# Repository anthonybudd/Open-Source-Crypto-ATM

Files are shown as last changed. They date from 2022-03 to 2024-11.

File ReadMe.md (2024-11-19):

# OSCA - Open-Source Crypto ATM

The Open-Source Crypto ATM, a Bitcoin ATM that someone with minimal electro-mechanical skill can build at home with parts from Amazon and hardware from Lowes. OSCA does not require you to disclose any personal information to use this ATM. The user inserts cash and the machine returns a cold wallet loaded with the desired amount of crypto-currency.

<p align="center">
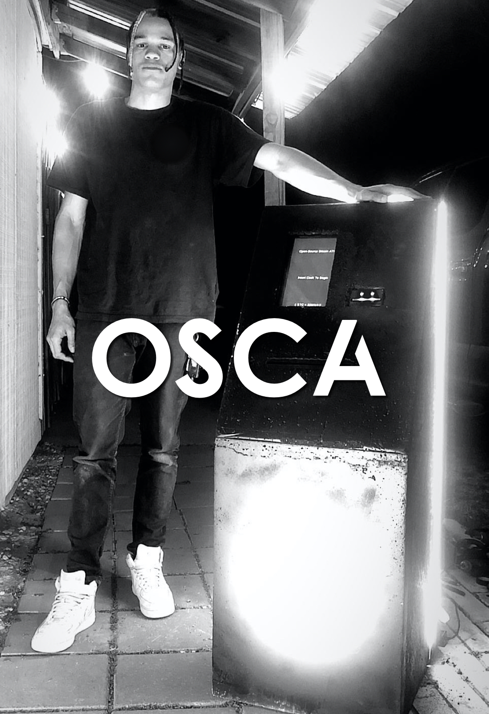
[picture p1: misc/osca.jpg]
OSCA
    
</p>

### Instructions
Detailed step-by-step instructions and a video tutorial are coming soon. However you can find all of the software and plans in this repo.
- [Build Instructions](https://github.com/anthonybudd/Open-Source-Crypto-ATM/blob/master/instructions/Instructions.md)

### Usecases

- Accept Bitcoin - Want to accept Bitcoin at your business? Use OSCA to provide your customers a easy way to purchase Bitcoin

- Passive Income - Use the commission feature to earn a commission on each transaction.
  
- Fungibility - Make crypto more fungibile by allowing anyone to anonymously convert hard fiat currency into cryptocurrency.

### How does it work?

OSCA is very simple to use. Simply insert the amount of cash you would like converted to Bitcoin then press the blue flashing button. 

<p align="center">
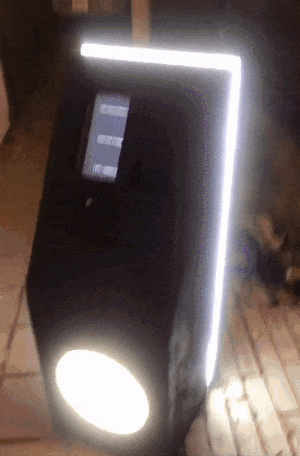
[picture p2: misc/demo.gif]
Demo
    
</p>

A paper wallet will be printed that is loaded with the desired amount of Bitcoin. Scan the status QR code to see your transaction on blockchain. Scan the withdraw QR code on the right to sweep the paper wallet. 

<p align="center">
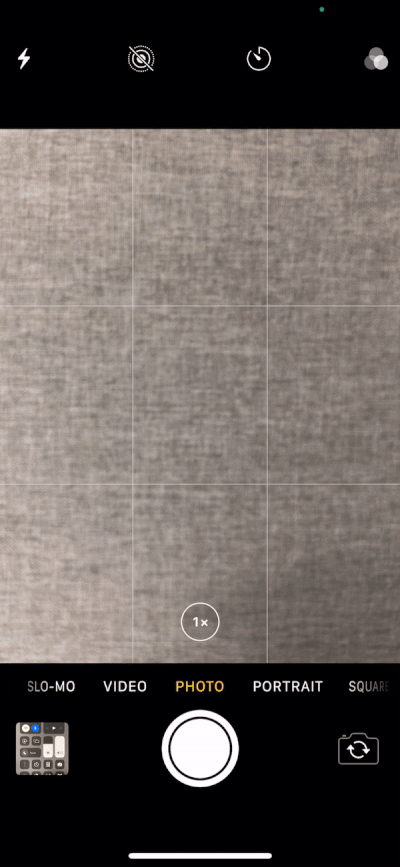
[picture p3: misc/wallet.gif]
    
</p>

### Motivation

Bitcoin and crypto in general have the power to revolutionise finance. However anonymously converting fiat currency into crypto is becoming harder and harder. All of the major crypto exchanges require disclosure of personal identifiable information. Even the Bitcoin ATMs at your local gas station require a cell phone number and an email address. Crypto-currencies are so much of a threat to the legacy banking system that the UK has banned Bitcoin ATMs outright. This concerns me because I believe if we remain on this course open-source technology like blockchain will become heavily regulated and corporatized.

The Open-Source Crypto ATM aims to remedy these issues by making it safe, easy and anonymous for anyone to convert hard fiat currency into digital cryptocurrency. The machine has been deliberately designed so someone with minimal electro-mechanical skill can build this ATM at home with a few off the shelf electronics and trip to the local hardware store.

By making this project open-source I hope others will contribute to this project and extend the software to work with other popular crypto-currencies. Over the long-term I hope that anonymous crypto ATMs will make crypto more accessible and fungible.

### FAQ

#### How can I trust this machine?

**YOU CAN’T**. I’ll say that again, you can’t trust this machine if you see it in the wild. A malicious actor could simply not load the paper wallet or save a copy of each private key it generates. So why build it then? My vision is that in the short to medium-term these kind of machines will be operated by independent businesses (gas stations, gun stores, smoke shops, etc) and the customers will trust the operator, not the machine per se. A user can easily test if the wallet is being loaded or not with a $5 transaction. Always remember to withdraw the value of the paper wallet to a secure wallet as soon as possible.

#### Why use paper wallets?

Paper wallets are controversial because they are considered outdated and unsecure, however I believe this is a perfect use case. While admittedly they have their drawbacks, paper wallets allow for the most anonymous method of exchanging cash for cryptocurrency. Any digital method could potentially expose the identity of the recipient. Furthermore any digital method of exchange would require the user to have a smartphone to use this machine, which not everybody has. I see no reason why cryptocurrencies must exist exclusively in the digital domain.

#### Why use concrete not metal?

Consider the Venn diagram of the parameters of this project. A) It must be easy to build B) Require minimal skill to build C) Must be cheap and extremely robust. While metal has obvious advantages (not least of which aesthetic), it requires skill to work with and expensive tools. Concrete is very cheap, it’s easy to work with and is exceptionally strong. Therefore concrete is the obvious choice.

#### Why Bitcoin? Why not Monero or Ethereum?

For better or for worse Bitcoin is the poster-child cryptocurrency. Its over a decade old, I bet your grandparents have heard about it at this point. Therefore I feel like that was the best cryptocurrency to start with.

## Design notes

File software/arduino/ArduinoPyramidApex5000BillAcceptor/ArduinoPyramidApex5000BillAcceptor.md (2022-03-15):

# ArduinoPyramidApex5000

This is a small program for using the Apex Pyramid 5000 bill acceptor via Serial.

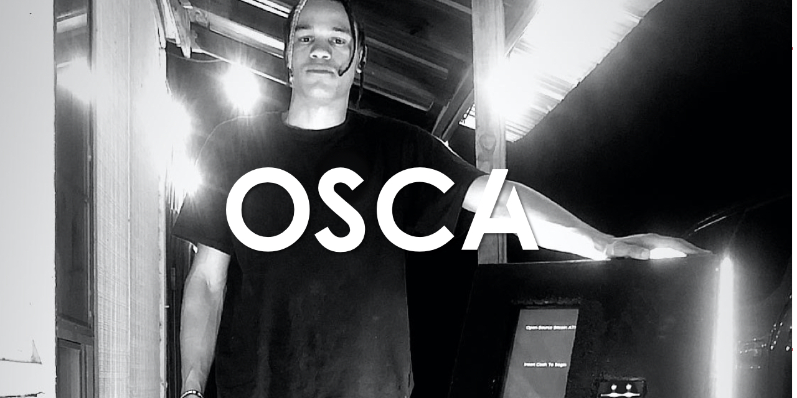
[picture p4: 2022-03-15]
misc/repo.jpg

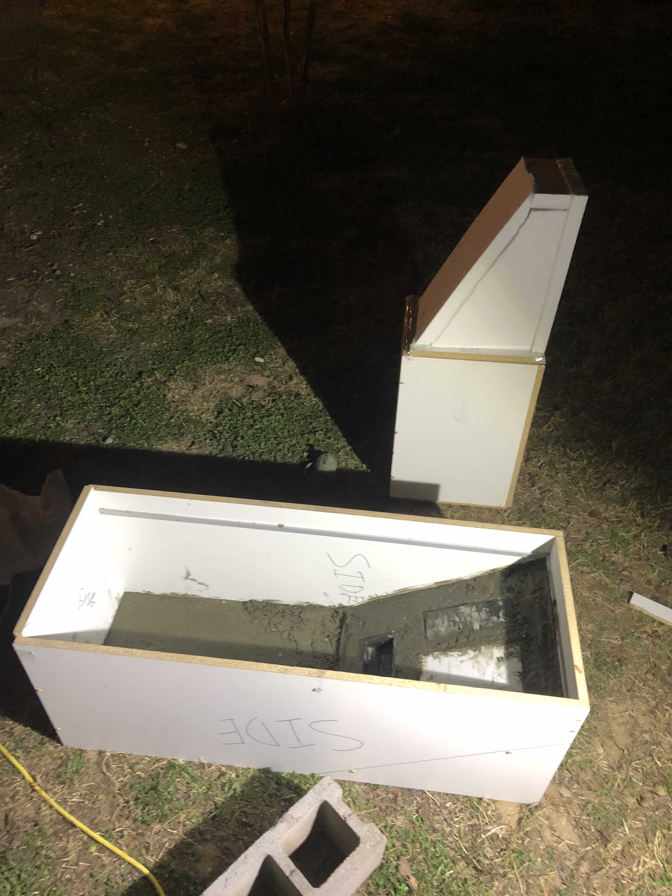
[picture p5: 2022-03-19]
misc/interior-and-exterior-mold.jpg

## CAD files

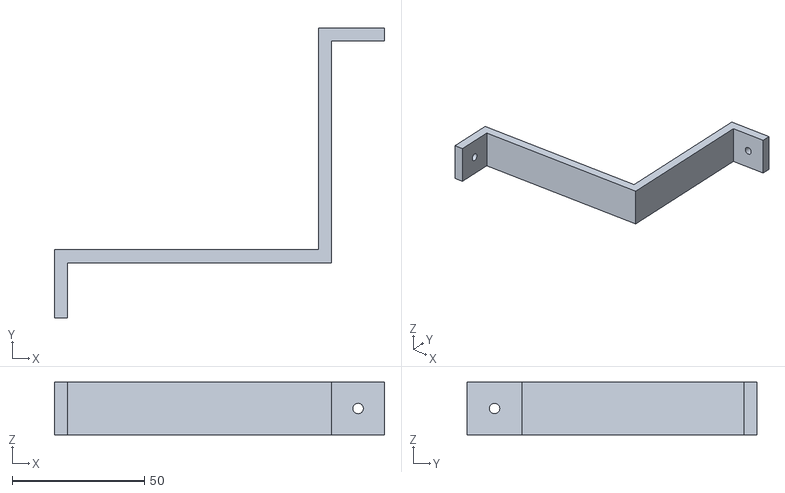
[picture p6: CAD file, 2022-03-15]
instructions/parts/Bill Accepter/Bill-Accepter-retention-arm.stl
125.0 x 109.9 x 20.0

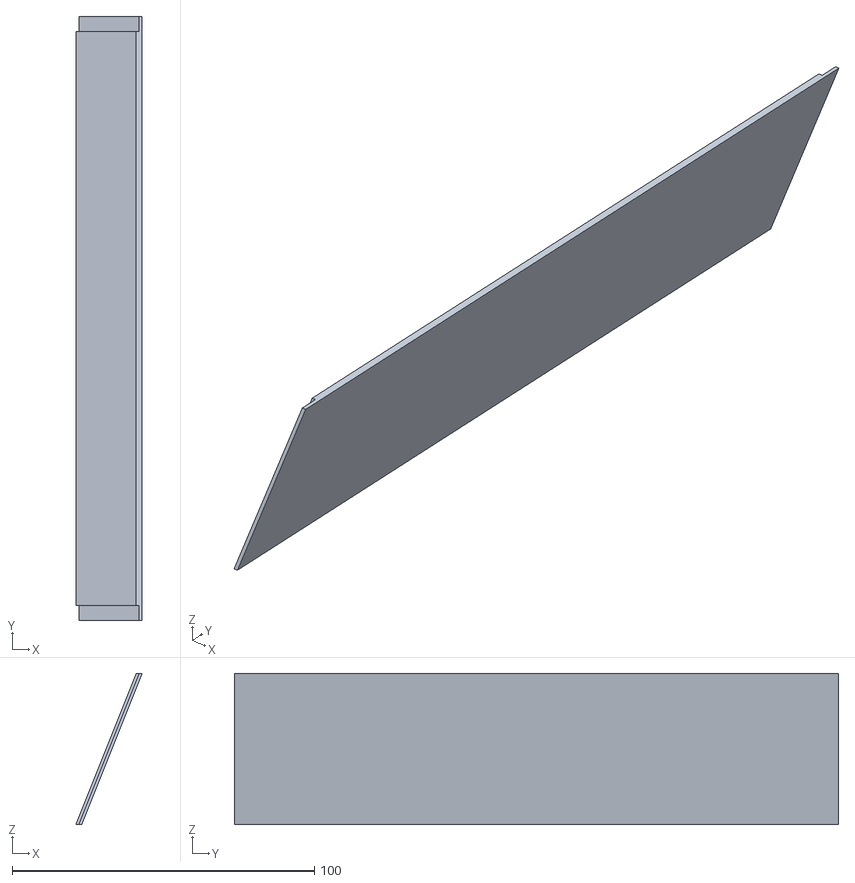
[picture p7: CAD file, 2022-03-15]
instructions/parts/Door/Side Inverted.stl
22.0 x 200.0 x 50.0

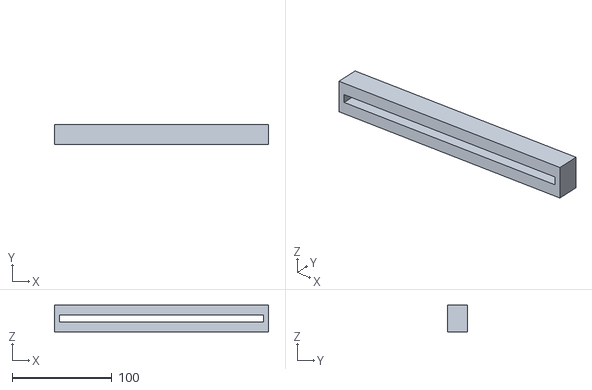
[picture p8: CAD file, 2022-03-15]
instructions/parts/Rollo/Rollo-Mouth.stl
215.0 x 20.0 x 27.0

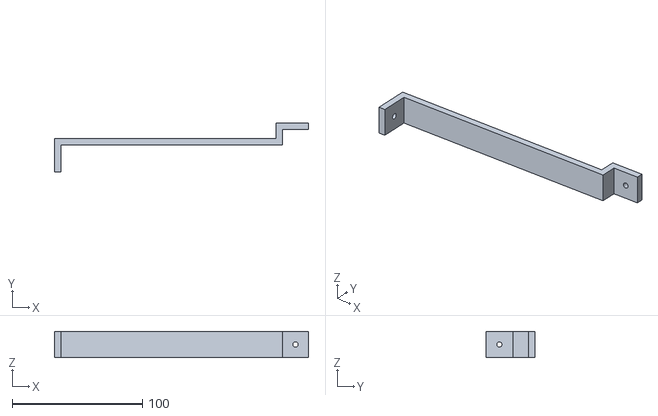
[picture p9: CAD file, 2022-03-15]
instructions/parts/Screen/Screen Retention Arm.stl
195.0 x 37.9 x 20.0

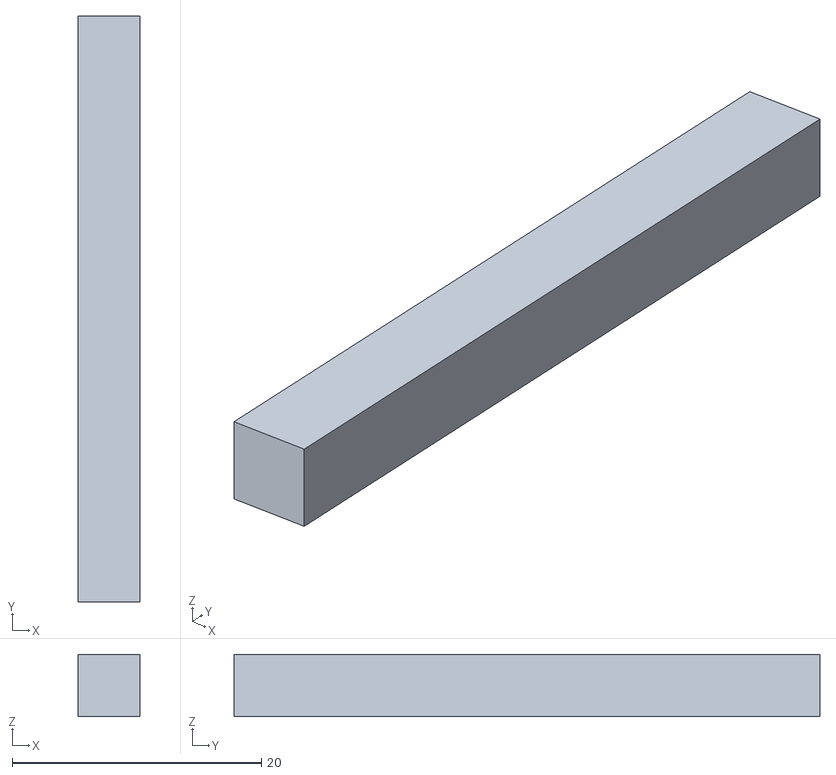
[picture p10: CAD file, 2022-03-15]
instructions/parts/Bill Accepter/bill accepter mold stand off.stl
5.00 x 47.0 x 5.00

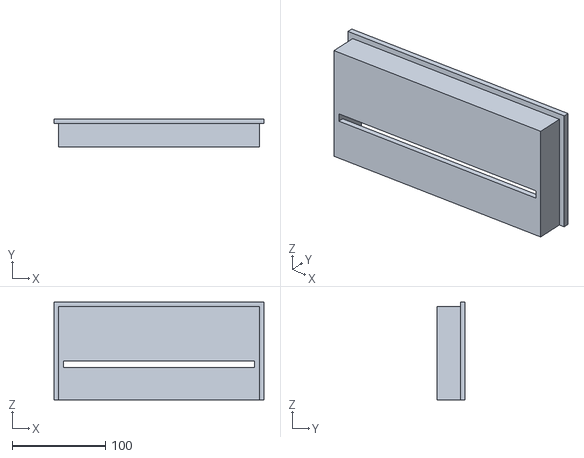
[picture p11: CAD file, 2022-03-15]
instructions/parts/Rollo/Rollo.stl
225.0 x 30.0 x 105.0

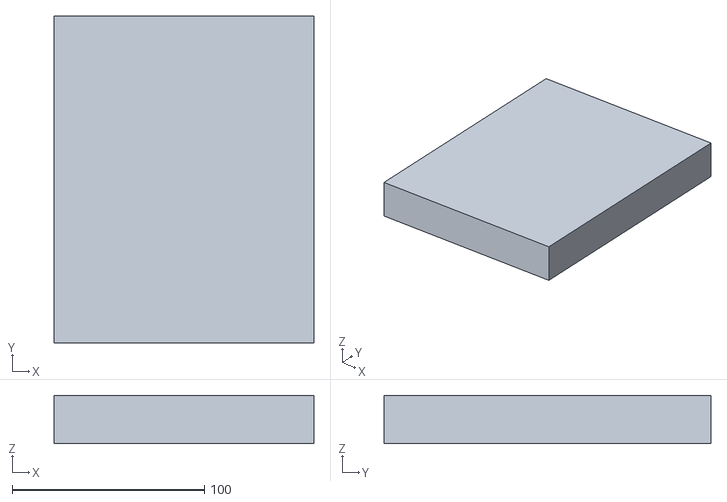
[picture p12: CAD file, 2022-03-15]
instructions/parts/Screen/screen mold.stl
135.0 x 170.0 x 25.0

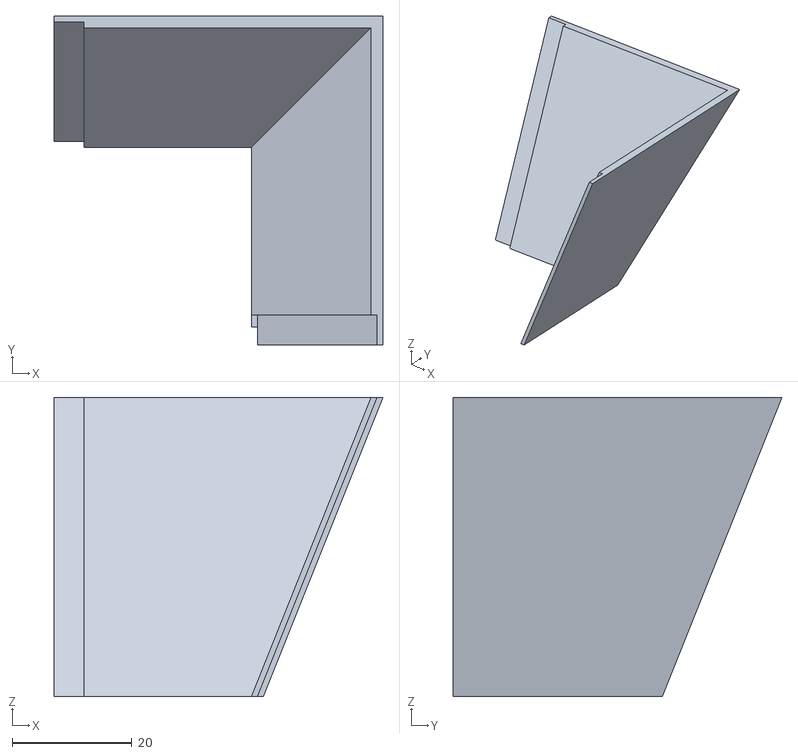
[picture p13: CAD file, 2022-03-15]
instructions/parts/Door/Corner.stl
55.0 x 55.0 x 50.0

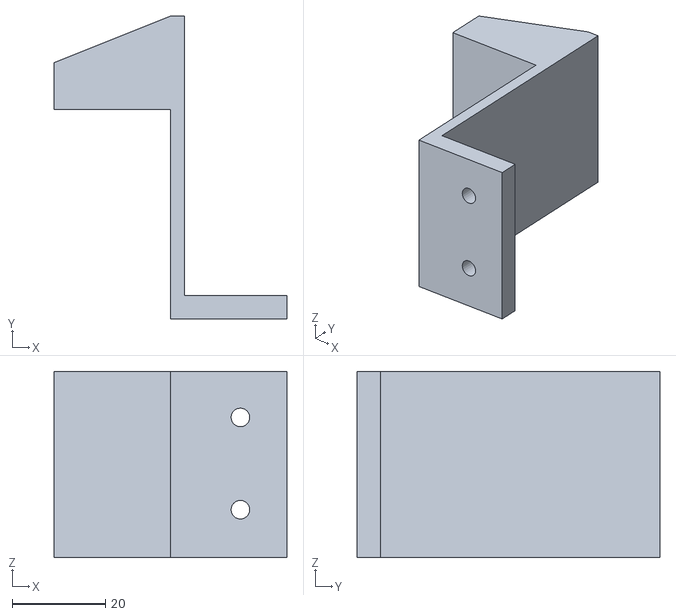
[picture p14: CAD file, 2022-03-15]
instructions/parts/Rollo/Rollo clip -10mm.stl
50.0 x 65.0 x 40.0

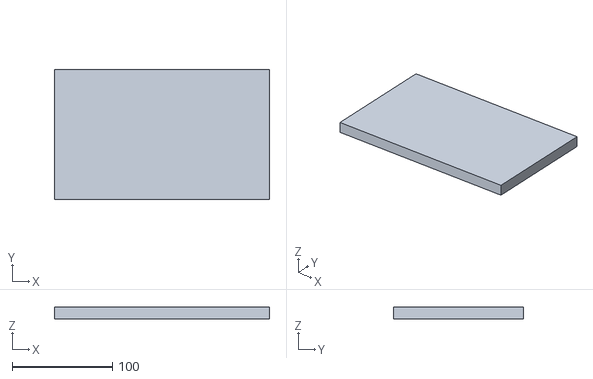
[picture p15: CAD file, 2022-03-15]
instructions/parts/Screen/viewport mold.stl
215.0 x 130.0 x 12.0

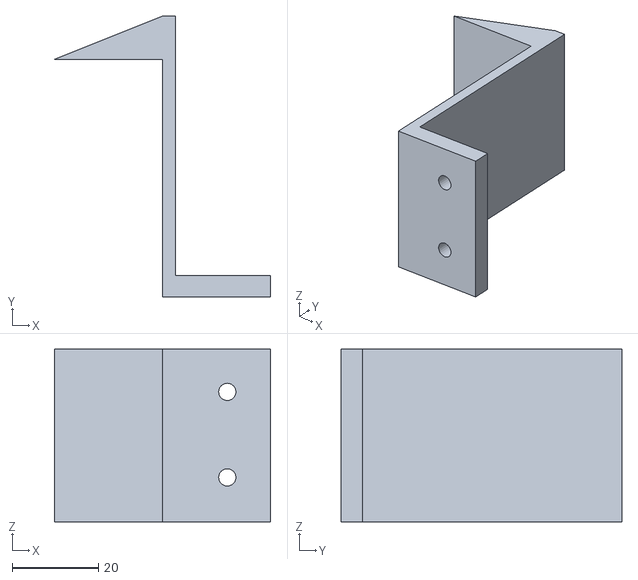
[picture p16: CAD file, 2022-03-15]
instructions/parts/Rollo/Rollo Retention Clip.stl
50.0 x 65.0 x 40.0

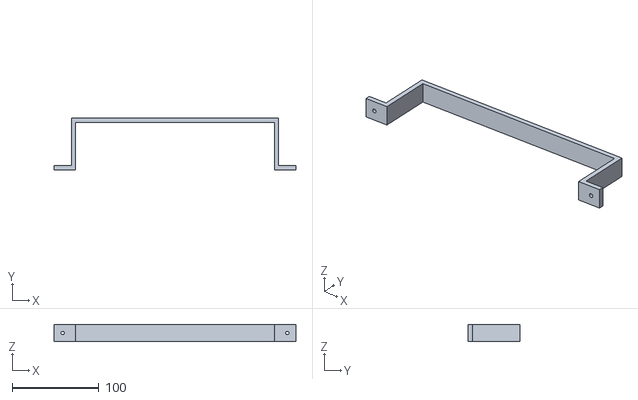
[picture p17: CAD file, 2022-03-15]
instructions/parts/Rollo/Rollo Retention Arm.stl
279.0 x 60.0 x 20.0

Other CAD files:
instructions/parts/Door/Side.stl
instructions/parts/Rollo/Rollo clip -5mm.stl
instructions/Case.skp
instructions/Case~.skp
instructions/parts/Bill Accepter/Bill Accepter.skp
instructions/parts/Bill Accepter/Bill-Accepter-retention-arm.skp
instructions/parts/Bill Accepter/Bill-Accepter-retention-arm~.skp
instructions/parts/Door/Corner.skp
instructions/parts/Door/Corner~.skp
instructions/parts/Rollo/Rollo.skp
instructions/parts/Rollo/Rollo~.skp
instructions/parts/Screen/Screen Retention Arm.skp
instructions/parts/Screen/Screen Retention Arm~.skp
instructions/parts/Screen/screen mold.skp
instructions/parts/Screen/viewport mold.skp
instructions/parts/Screen/viewport mold~.skp

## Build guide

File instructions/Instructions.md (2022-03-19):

# Instructions
*Detailed step by step instructions and a video tutorial are coming soon.*

I will be writing more detailed instructions as I develop this project. Below is a brief overview on how you can build an OSCA machine.

<!-- 
### Parts
| Name        | Price | Link |
| ----------- | ----- ------ | ----------- |
| Pyramid APEX 7000       | $200       |  |
| Paragraph   | Text        |  |

### Tools
| Name | Price | Link |
| --- | --- | --- |
| Pyramid APEX 7000 | $200 |  |
| Paragraph | Text |  | -->

### Phase 1
I recommend that you build OSCA using the same three phase approach I developed it. First buy the electronics and test the software, second build the cast and pour the concrete, finally mount the electronics and paint.

#### Arduino and Bill Acceptor
First load the provided Arduino sketch onto the Arduino nano. Connect the button  and the Apex 7000 bill acceptor as shown in the provided schematic.

Using the Arduino IDE serial monitor test that the Arduino is outputting the expected strings. Insert a bill into the bill acceptor and you should see the dollar amount display on the serial monitor. When you press the button the serial monitor should display the string “RESET”

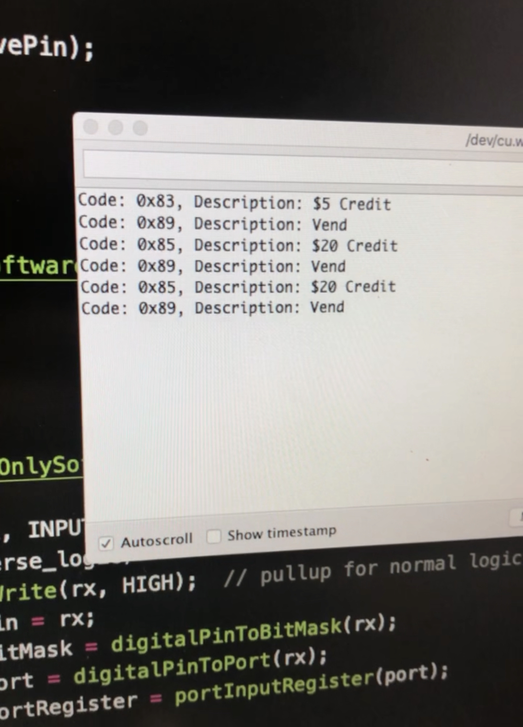
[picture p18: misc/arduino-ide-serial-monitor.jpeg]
Arduino IDE serial monitor


#### Pi
Run the provided bash commands provided in [App.md](https://github.com/anthonybudd/Open-Source-Crypto-ATM/blob/master/software/app/App.md) to set up your Pi and make the python script auto-run.

#### Printer/CUPS
Install cups and install the provided rollo Linux driver. Do a test print using the CLI and an example 4x6 label pdf to confirm that the printer is correctly set-up.
`lp -h localhost:631 ~/test.pdf`

#### Cellular Router
Insert a sim into the cellular router and connect the LAN 2 port to the raspberry Pi’s Ethernet port. Confirm that you have a internet connection by visiting a website using the pi’s browser.

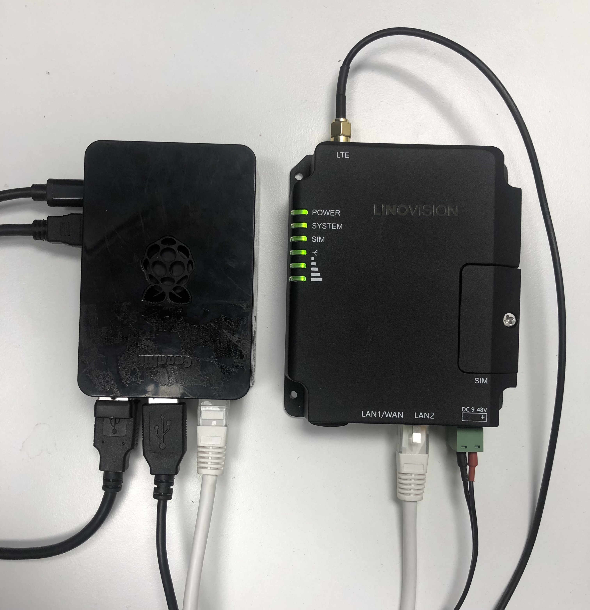
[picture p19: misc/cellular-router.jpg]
Cellular router and Pi


*I will be addressing the need for a 4G device in a upcoming project*

#### Battery
Connect all of the electronics to the battery and test that the system can power up, connect to the internet, boot the python GUI and it can successfully make a transaction.

### Phase 2
Go to your local hardware store and buy 3/4 lined 8x4 wood sheets. Have the store cut the wood as shown in the [provided designs](https://github.com/anthonybudd/Open-Source-Crypto-ATM/blob/master/instructions/case.png). 

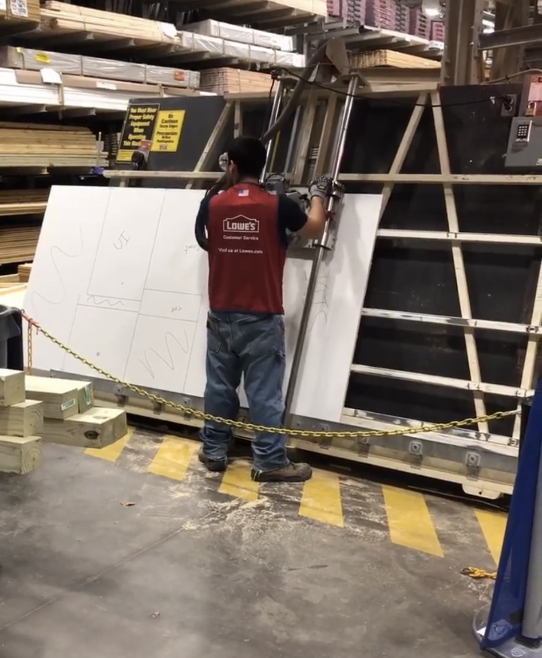
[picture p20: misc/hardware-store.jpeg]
Harware Store


Using a 3D printer print the casting parts for the machine. Use a hot glue gun to stick the molds to the internal side of the UI face.

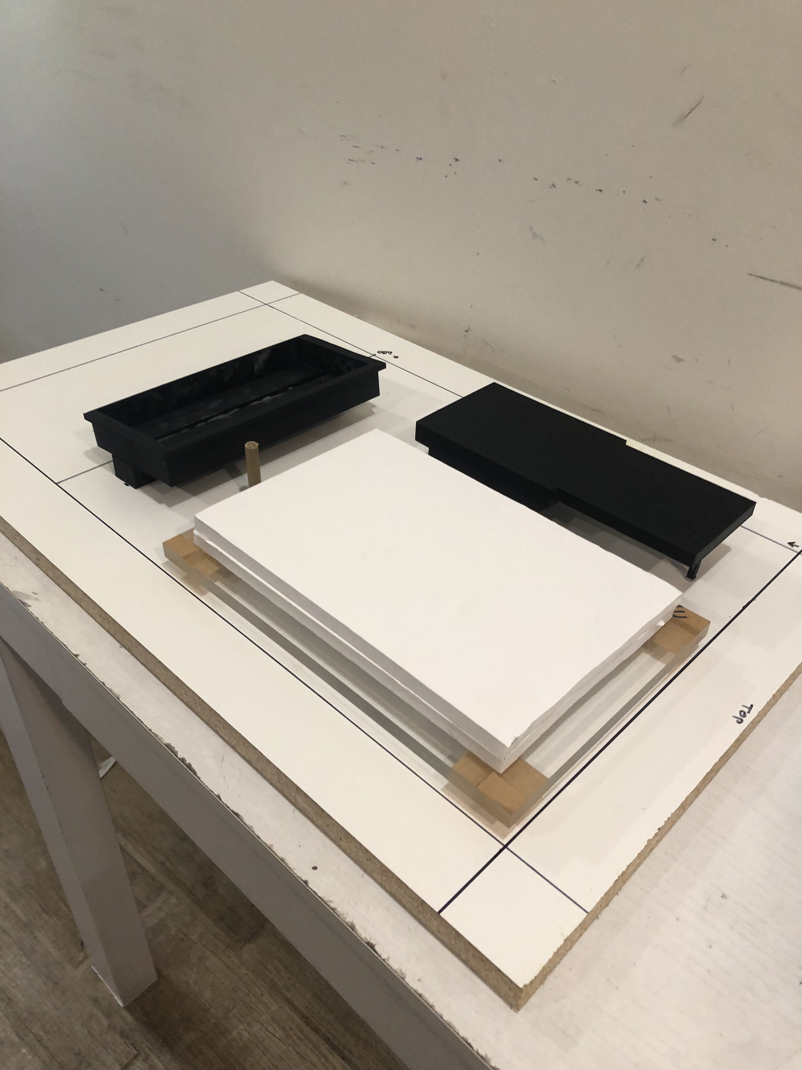
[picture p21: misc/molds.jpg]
3D Printed Molds


Screw the wood together to form the outer cast. 

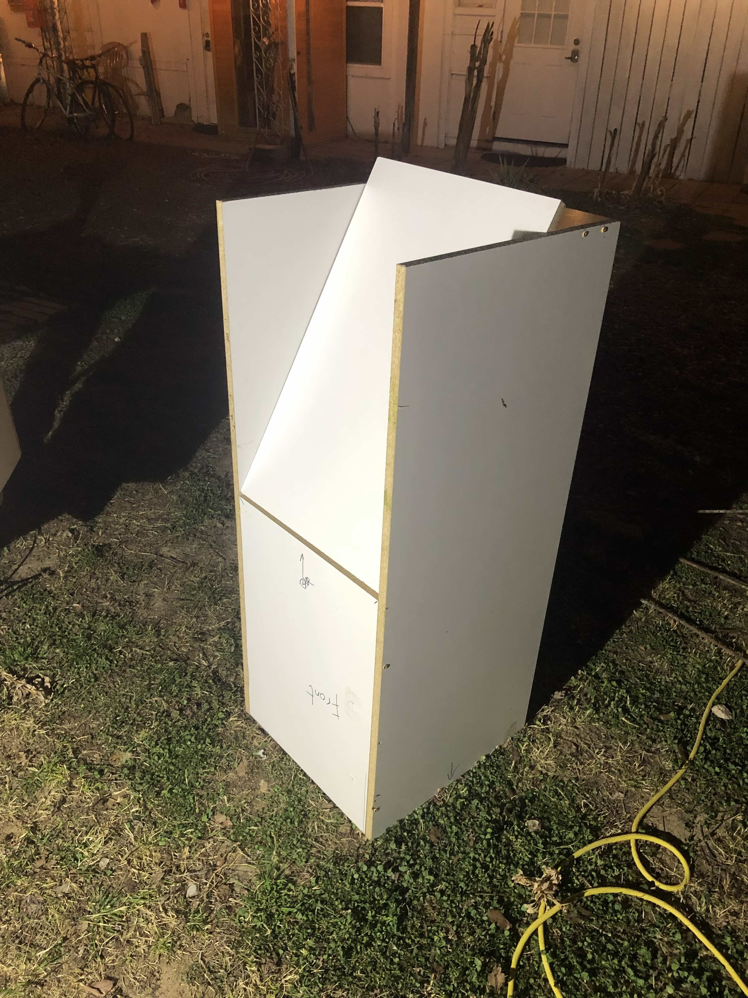
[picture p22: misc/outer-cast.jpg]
Outer Cast


Screw the interior mold together and glue on the polystyrene foam insert.

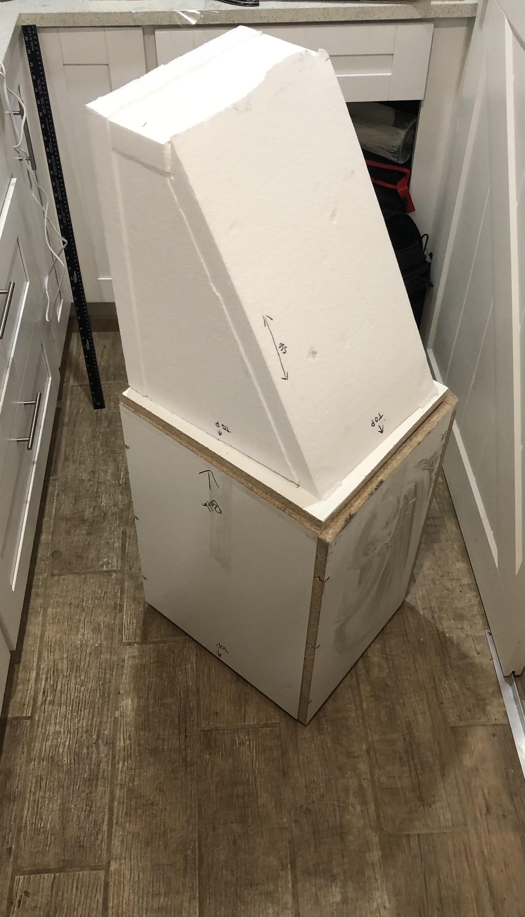
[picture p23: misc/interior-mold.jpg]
Interior Mold


Mix the concrete, start by packing the concrete into the small areas between the 3d printed molds. Wait an hour for the UI face to begin to set then lay the concrete for the front face.

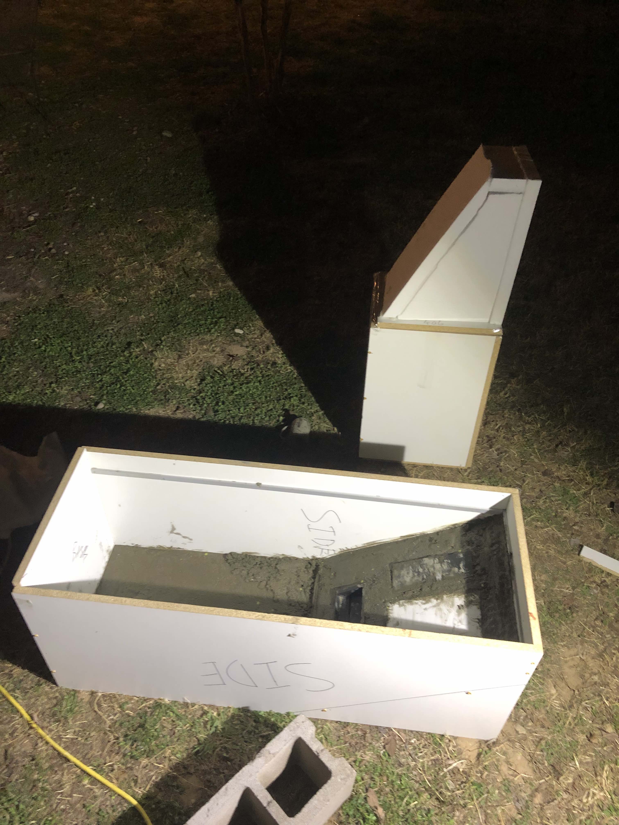
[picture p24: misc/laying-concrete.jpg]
First Concrete


Finally insert the interior mold into the exterior mold and fill the remainiung space with concrtete. Wait 24 hours for the cast to dry.

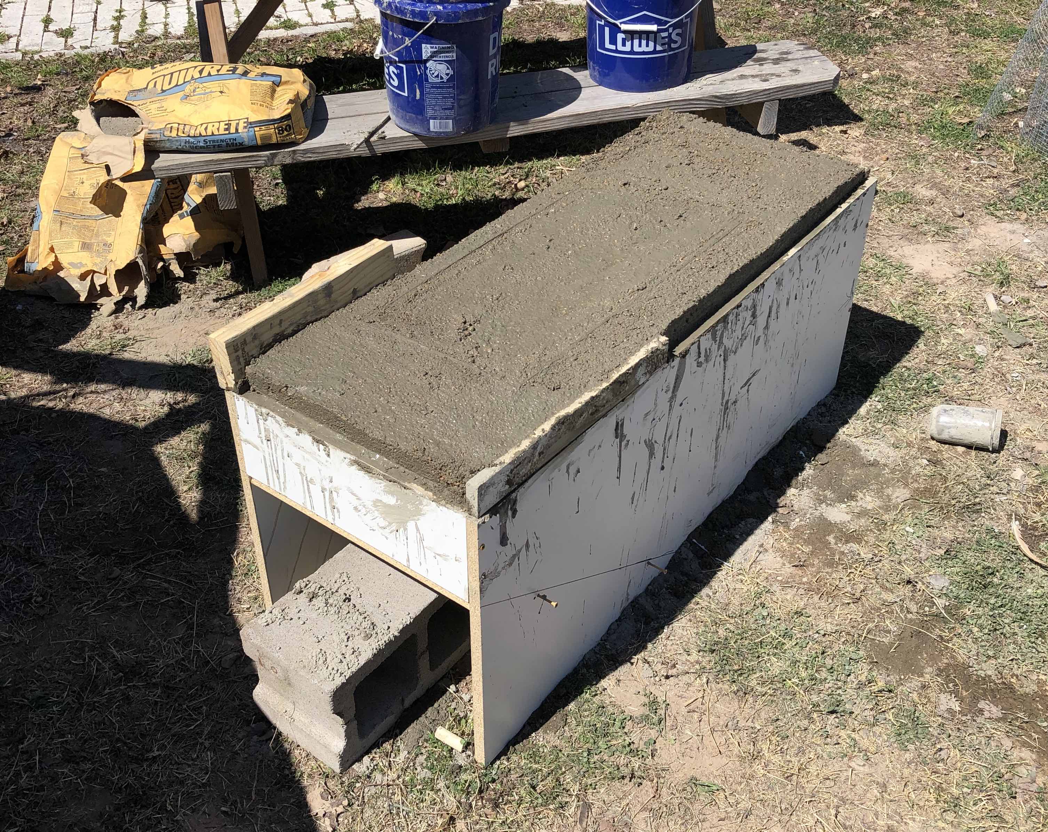
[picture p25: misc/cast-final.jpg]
Cast Final


### Phase 3
Finally paint and mount the optional LED strips. Place the electronics inside the case. Power up the ATM and lock the door, Do a test run.

Congratulations you have build a Open-Source Crypto ATM.

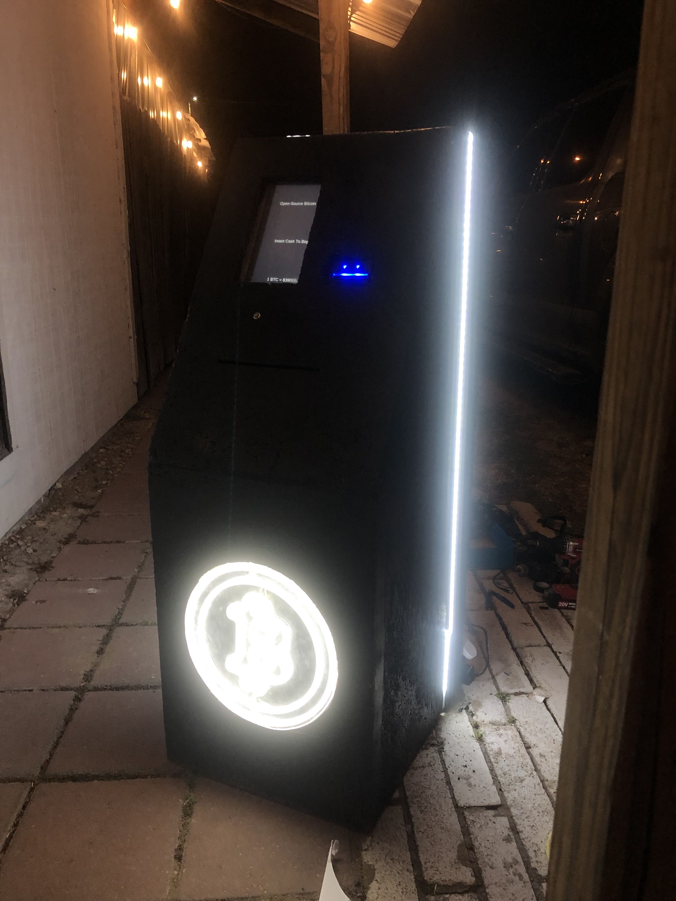
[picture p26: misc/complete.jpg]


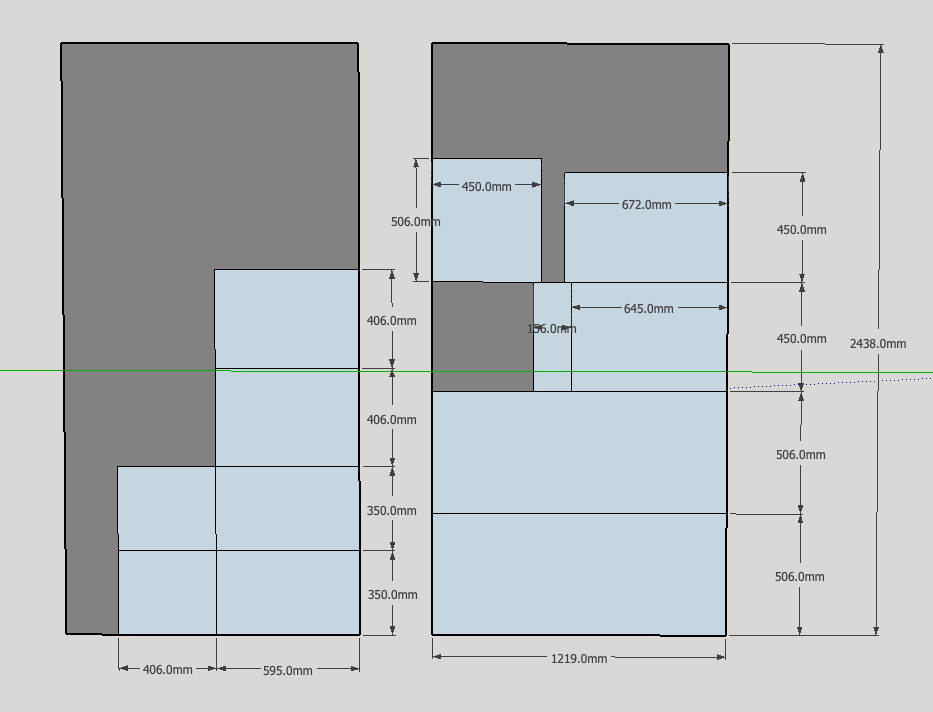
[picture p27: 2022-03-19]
instructions/case.png

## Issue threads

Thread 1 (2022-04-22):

Missing Schematics

sunrisellc, 2022-04-22:
Hello,

You refer to a wiring schematic in the instructions but it does not appear to be included with the files.

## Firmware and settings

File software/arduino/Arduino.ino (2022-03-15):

#include <Arduino.h>
#include <ReceiveOnlySoftwareSerial.h>
#include <Apex5400BillAcceptor.h>

#define PIN_ENABLE 7 // To Pin 12 (violet)
#define PIN_INTERRUPT_LINE 8 // To Pin 2 (orange)
#define PIN_SEND_LINE 9 // To Pin 14 (blue/white)
#define PIN_TTL_RX 10 // to Pin 5 (green)

Apex5400BillAcceptor *billAcceptor;

int code;
bool hasCredit = false;
bool isPrinting = false;
int ledPin = 6;
int switchPin = 5;
int ledState = LOW;
unsigned long previousMillis = 0;
const long interval = 500; 
int incomingByte = 0;

const byte numChars = 32;
char receivedChars[numChars];
boolean newData = false;

void setup() {
  pinMode(ledPin, OUTPUT);
  pinMode(switchPin, INPUT);
  Serial.begin(9600);
  billAcceptor = new Apex5400BillAcceptor(PIN_ENABLE, PIN_INTERRUPT_LINE, PIN_SEND_LINE, PIN_TTL_RX);    
  billAcceptor->enable();
  Serial.println("READY");
}

void loop() {
  
  // Wait for credit
  if (isPrinting == false) {
    if (code = billAcceptor->checkForBill()) {
      Serial.println(billAcceptor->getDescription(code));

      switch(code) {
        case 0x81:
        case 0x83:
        case 0x84:
        case 0x85:
        case 0x86:
        case 0x87:
          hasCredit = true;
          billAcceptor->disable(); // Sync LED flashing on button and Apex
          billAcceptor->enable();
          break;
      }
    }
  }

  // We have credit, wait for button press
  if (hasCredit == true) {
    flash();
    
    if (digitalRead(switchPin) == HIGH) {
      Serial.println("PRINT");
      billAcceptor->disable();
      digitalWrite(ledPin, LOW);
      isPrinting = true;
      hasCredit = false;
    }
  }

  // Always listen for "RESET" signal
  isResetSigal();
  recvWithEndMarker(); 
}

void flash(){
  unsigned long currentMillis = millis();
  if (currentMillis - previousMillis >= interval) {
    previousMillis = currentMillis;

    if (ledState == LOW) {
      ledState = HIGH;
    } else {
      ledState = LOW;
    }

    digitalWrite(ledPin, ledState);
  }
}

void recvWithEndMarker() {
  static byte ndx = 0;
  char endMarker = '\n';
  char rc;
 
  while (Serial.available() > 0 && newData == false) {
    rc = Serial.read();
    
    if (rc != endMarker) {
      receivedChars[ndx] = rc;
      ndx++;
      if (ndx >= numChars) {
        ndx = numChars - 1;
      }
    } else {
      receivedChars[ndx] = '\0'; // terminate the string
      ndx = 0;
      newData = true;
    }
  }
}

void isResetSigal() {
  if (newData == true) {
    String input(receivedChars);
    Serial.println(input);
    if (input == "RESET") {
      reset();
    }
    newData = false;
  }
}

void reset(){
  Serial.println("RESETTING");
  billAcceptor->enable();
  isPrinting = false;
  hasCredit = false;
}

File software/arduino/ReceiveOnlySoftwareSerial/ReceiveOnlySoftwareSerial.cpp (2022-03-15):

/*

ReceiveOnlySoftwareSerial - adapted from SoftwareSerial by Joe C 17 May 2014

ReceiveOnlySoftwareSerial.cpp (formerly SoftSerial.cpp) - 
Multi-instance software serial library for Arduino/Wiring
-- Interrupt-driven receive and other improvements by ladyada
   (http://ladyada.net)
-- Tuning, circular buffer, derivation from class Print/Stream,
   multi-instance support, porting to 8MHz processors,
   various optimizations, PROGMEM delay tables, inverse logic and 
   direct port writing by Mikal Hart (http://www.arduiniana.org)
-- Pin change interrupt macros by Paul Stoffregen (http://www.pjrc.com)
-- 20MHz processor support by Garrett Mace (http://www.macetech.com)
-- ATmega1280/2560 support by Brett Hagman (http://www.roguerobotics.com/)

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
The latest version of this library can always be found at
http://arduiniana.org.
*/

// When set, _DEBUG co-opts pins 11 and 13 for debugging with an
// oscilloscope or logic analyzer.  Beware: it also slightly modifies
// the bit times, so don't rely on it too much at high baud rates
#define _DEBUG 0
#define _DEBUG_PIN1 11
#define _DEBUG_PIN2 13
// 
// Includes
// 
#include <avr/interrupt.h>
#include <avr/pgmspace.h>
#include <Arduino.h>
#include <ReceiveOnlySoftwareSerial.h>
//
// Lookup table
//
typedef struct _DELAY_TABLE
{
  long baud;
  unsigned short rx_delay_centering;
  unsigned short rx_delay_intrabit;
  unsigned short rx_delay_stopbit;
  unsigned short tx_delay;
} DELAY_TABLE;

#if F_CPU == 16000000

static const DELAY_TABLE PROGMEM table[] = 
{
  //  baud    rxcenter   rxintra    rxstop    tx
  { 115200,   1,         17,        17,       12,    },
  { 57600,    10,        37,        37,       33,    },
  { 38400,    25,        57,        57,       54,    },
  { 31250,    31,        70,        70,       68,    },
  { 28800,    34,        77,        77,       74,    },
  { 19200,    54,        117,       117,      114,   },
  { 14400,    74,        156,       156,      153,   },
  { 9600,     114,       236,       236,      233,   },
  { 4800,     233,       474,       474,      471,   },
  { 2400,     471,       950,       950,      947,   },
  { 1200,     947,       1902,      1902,     1899,  },
  { 600,      1902,      3804,      3804,     3800,  },
  { 300,      3804,      7617,      7617,     7614,  },
};

const int XMIT_START_ADJUSTMENT = 5;

#elif F_CPU == 8000000

static const DELAY_TABLE table[] PROGMEM = 
{
  //  baud    rxcenter    rxintra    rxstop  tx
  { 115200,   1,          5,         5,      3,      },
  { 57600,    1,          15,        15,     13,     },
  { 38400,    2,          25,        26,     23,     },
  { 31250,    7,          32,        33,     29,     },
  { 28800,    11,         35,        35,     32,     },
  { 19200,    20,         55,        55,     52,     },
  { 14400,    30,         75,        75,     72,     },
  { 9600,     50,         114,       114,    112,    },
  { 4800,     110,        233,       233,    230,    },
  { 2400,     229,        472,       472,    469,    },
  { 1200,     467,        948,       948,    945,    },
  { 600,      948,        1895,      1895,   1890,   },
  { 300,      1895,       3805,      3805,   3802,   },
};

const int XMIT_START_ADJUSTMENT = 4;

#elif F_CPU == 20000000

// 20MHz support courtesy of the good people at macegr.com.
// Thanks, Garrett!

static const DELAY_TABLE PROGMEM table[] =
{
  //  baud    rxcenter    rxintra    rxstop  tx
  { 115200,   3,          21,        21,     18,     },
  { 57600,    20,         43,        43,     41,     },
  { 38400,    37,         73,        73,     70,     },
  { 31250,    45,         89,        89,     88,     },
  { 28800,    46,         98,        98,     95,     },
  { 19200,    71,         148,       148,    145,    },
  { 14400,    96,         197,       197,    194,    },
  { 9600,     146,        297,       297,    294,    },
  { 4800,     296,        595,       595,    592,    },
  { 2400,     592,        1189,      1189,   1186,   },
  { 1200,     1187,       2379,      2379,   2376,   },
  { 600,      2379,       4759,      4759,   4755,   },
  { 300,      4759,       9523,      9523,   9520,   },
};

//const int XMIT_START_ADJUSTMENT = 6;

#else

#error This version of SoftwareSerial supports only 20, 16 and 8MHz processors

#endif

//
// Statics
//
ReceiveOnlySoftwareSerial *ReceiveOnlySoftwareSerial::active_object = 0;
char ReceiveOnlySoftwareSerial::_receive_buffer[_SS_MAX_RX_BUFF]; 
volatile uint8_t ReceiveOnlySoftwareSerial::_receive_buffer_tail = 0;
volatile uint8_t ReceiveOnlySoftwareSerial::_receive_buffer_head = 0;

//
// Debugging
//
// This function generates a brief pulse
// for debugging or measuring on an oscilloscope.
inline void DebugPulse(uint8_t pin, uint8_t count)
{
#if _DEBUG
  volatile uint8_t *pport = portOutputRegister(digitalPinToPort(pin));

  uint8_t val = *pport;
  while (count--)
  {
    *pport = val | digitalPinToBitMask(pin);
    *pport = val;
  }
#endif
}

//
// Private methods
//

/* static */ 
inline void ReceiveOnlySoftwareSerial::tunedDelay(uint16_t delay) { 
  uint8_t tmp=0;

  asm volatile("sbiw    %0, 0x01 \n\t"
    "ldi %1, 0xFF \n\t"
    "cpi %A0, 0xFF \n\t"
    "cpc %B0, %1 \n\t"
    "brne .-10 \n\t"
    : "+r" (delay), "+a" (tmp)
    : "0" (delay)
    );
}

// This function sets the current object as the "listening"
// one and returns true if it replaces another 
bool ReceiveOnlySoftwareSerial::listen()
{
  if (active_object != this)
  {
    _buffer_overflow = false;
    uint8_t oldSREG = SREG;
    cli();
    _receive_buffer_head = _receive_buffer_tail = 0;
    active_object = this;
    SREG = oldSREG;
    return true;
  }

  return false;
}

//
// The receive routine called by the interrupt handler
//
void ReceiveOnlySoftwareSerial::recv()
{
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
